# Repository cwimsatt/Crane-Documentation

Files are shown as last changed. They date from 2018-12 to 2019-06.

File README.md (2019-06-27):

---
description: Information on your M3D Crane Series printer.
---

# Welcome

Welcome and thank you for choosing the M3D Crane series of printers! This is the getting started / quick-start guide for the Crane Series 3D Printer. First select the Model style of M3D Crane you have purchased and you will be directed to the Quick Start Guide that matches your new printer.

NEW - July 2019 WalkThrough / Crash Course: For users setting up their quad head for the first time and looking to gain a deep understanding of the system to get the best results, start [here](https://coda.io/d/M3D-Official-Troubleshooting-Self-Help-Guide_dzE73kMbIAL/Quad-Expert-Crash-Course_sudLH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).

For troubleshooting please visit the [Self-help guide](https://coda.io/d/M3D-Public-Coda-Self-Help-Support_dzE73kMbIAL/Crane-Troubleshooting_suMmY#_lu4jO)

| \*\*\*\*[**The Crane Bowden**](https://crane.printm3d.com/crane-bowden-guide/crane-bowden-unboxing-assembly)\*\*\*\* | [**The Crane Dual**](https://crane.printm3d.com/crane-dual/unboxing-and-assembly)\*\*\*\* | \*\*\*\*[**The Crane Quad**](https://crane.printm3d.com/crane-quad-guide/unboxing-and-assembly)\*\*\*\* |
| :---: | :---: | :---: |

<table>
  <thead>
    <tr>
      <th style="text-align:center">
        gras
      </th>
      <th style="text-align:left">
        
        <p>
          test
        </p>
      </th>
      <th style="text-align:center">
        gras
      </th>
    </tr>
  </thead>
  <tbody></tbody>
</table>| Quick Links -- Bowden | Quick Links--Dual | Quick Links -- Quad |
| :---: | :---: | :---: |
| [Assembly Guide](https://crane.printm3d.com/crane-bowden-guide/crane-bowden-unboxing-assembly) | [Assembly Guide](https://crane.printm3d.com/crane-dual/unboxing-and-assembly) | [Assembly Guide](https://crane.printm3d.com/crane-quad-guide/unboxing-and-assembly) |
| [Network Setup](https://crane.printm3d.com/crane-bowden-guide/first-time-network-setup) | [Network Setup](https://crane.printm3d.com/crane-dual/first-time-network-setup) | [Network Setup](https://crane.printm3d.com/crane-quad-guide/first-time-network-setup) |
| [LCD Menu Navigation](https://crane.printm3d.com/crane-bowden-guide/lcd-menu-navigation) | [LCD Menu Navigation](https://crane.printm3d.com/crane-dual/lcd-menu-navigation) | [LCD Menu Navigation ](https://crane.printm3d.com/crane-quad-guide/lcd-menu-navigation)  |
| [Duet Web Control First Look](https://crane.printm3d.com/crane-bowden-guide/intro-to-duet-web-control) | [Duet Web Control First Look ](https://crane.printm3d.com/crane-dual/duet-web-control-first-look) | [Duet Web Control First Look](https://crane.printm3d.com/crane-quad-guide/first-look-at-duet-web-control-interface)  |
| [Bed Leveling](https://crane.printm3d.com/crane-bowden-guide/manual-bed-leveling) | [Bed Leveling](https://crane.printm3d.com/crane-dual/manual-bed-leveling-assistant)  | [Bed Leveling](https://crane.printm3d.com/crane-quad-guide/manual-bed-leveling-assistant) |
| [Bed/Nozzle Control](https://crane.printm3d.com/crane-bowden-guide/heating-the-bed-and-the-nozzle) | [Bed/Nozzle Control](https://crane.printm3d.com/crane-dual/heating-the-bed-and-the-nozzle) | [Bed/Nozzle Control](https://crane.printm3d.com/crane-quad-guide/heating-the-bed-and-the-nozzle) |
| [Loading/Unloading Filament](https://crane.printm3d.com/crane-bowden-guide/loading-and-unloading-filament) | [Loading/Unloading Filament](https://crane.printm3d.com/crane-dual/loading-and-unloading-filament) | [Loading/Unloading Filament](https://crane.printm3d.com/crane-quad-guide/loading-and-unloading-filament) |
| [Slicing your Model](https://crane.printm3d.com/crane-bowden-guide/slicing-and-printing-your-first-model) | [Slicing your Model](https://crane.printm3d.com/crane-dual/finding-and-slicing-your-model) | [Slicing your Model](https://crane.printm3d.com/crane-quad-guide/finding-and-slicing-a-model) |
| [Your First Print](https://crane.printm3d.com/crane-bowden-guide/first-print) | [Your First Print](https://crane.printm3d.com/crane-dual/first-print) | [Your First Print](https://crane.printm3d.com/crane-bowden-guide/first-print) |

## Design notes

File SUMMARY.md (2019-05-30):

# Table of contents

* [Welcome](README.md)
* [Warnings](warnings.md)
* [Coda For Troubleshooting](coda-troubleshooting.md)

## Crane Bowden Guide

* [Unboxing/Assembly](crane-bowden-guide/crane-bowden-unboxing-assembly.md)
* [First time Network Setup](crane-bowden-guide/first-time-network-setup.md)
* [LCD Menu Navigation](crane-bowden-guide/lcd-menu-navigation.md)
* [First look at Duet Web Control](crane-bowden-guide/intro-to-duet-web-control.md)
* [Bed Leveling](crane-bowden-guide/manual-bed-leveling.md)
* [Heating the Bed and the Nozzle](crane-bowden-guide/heating-the-bed-and-the-nozzle.md)
* [Loading and Unloading Filament](crane-bowden-guide/loading-and-unloading-filament.md)
* [Finding and Slicing a Model](crane-bowden-guide/slicing-and-printing-your-first-model.md)
* [First Print](crane-bowden-guide/first-print.md)

## Crane Quad Guide

* [Unboxing and Assembly](crane-quad-guide/unboxing-and-assembly.md)
* [First time Network Setup](crane-quad-guide/first-time-network-setup.md)
* [LCD Menu Navigation](crane-quad-guide/lcd-menu-navigation.md)
* [First Look at Duet Web Control Interface](crane-quad-guide/first-look-at-duet-web-control-interface.md)
* [Bed Leveling](crane-quad-guide/manual-bed-leveling-assistant.md)
* [Heating the Bed and the Nozzle](crane-quad-guide/heating-the-bed-and-the-nozzle.md)
* [Loading and Unloading Filament](crane-quad-guide/loading-and-unloading-filament.md)
* [Finding and Slicing a Model](crane-quad-guide/finding-and-slicing-a-model.md)
* [First Print](crane-quad-guide/first-print.md)

## Crane Dual

* [Unboxing and Assembly](crane-dual/unboxing-and-assembly.md)
* [First time Network Setup](crane-dual/first-time-network-setup.md)
* [LCD Menu Navigation](crane-dual/lcd-menu-navigation.md)
* [Duet Web Control First Look](crane-dual/duet-web-control-first-look.md)
* [Bed Leveling](crane-dual/manual-bed-leveling-assistant.md)
* [Heating the bed and the Nozzle](crane-dual/heating-the-bed-and-the-nozzle.md)
* [Loading and Unloading Filament](crane-dual/loading-and-unloading-filament.md)
* [Finding and Slicing Your Model](crane-dual/finding-and-slicing-your-model.md)
* [First Print](crane-dual/first-print.md)

## SD card and Firmware

* [Accessing Your SD Card](sd-card-and-firmware/accessing-your-sd-card.md)
* [SD card Structure](sd-card-and-firmware/sd-card-structure.md)
* [Firmware/Configuration](sd-card-and-firmware/updating-firmware.md)

## Advanced Tuning M3D Crane Series

* [Part Prints M3D Crane Series](advanced-tuning-m3d-crane-series/part-prints-m3d-crane-series.md)
* [Introduction to G-Code Commands](advanced-tuning-m3d-crane-series/beginner-introduction-to-g-code-commands.md)
* [Duet Web Control Bed Leveling Assistant](advanced-tuning-m3d-crane-series/duet-web-control-bed-leveling-assistant.md)
* [Important G-Code Commands](advanced-tuning-m3d-crane-series/important-g-code-commands.md)
* [Pro Tuning Guide](advanced-tuning-m3d-crane-series/tuning-guide.md)
* [Temperature Calibration](advanced-tuning-m3d-crane-series/temperature-calibration.md)
* [Adjusting Homing Macros](advanced-tuning-m3d-crane-series/adjusting-homing-macros.md)
* [Filament Extrusion Rate](advanced-tuning-m3d-crane-series/filament-extrusion-rate.md)
* [ABS-R Success Guide](advanced-tuning-m3d-crane-series/abs-r-success-guide.md)
* [In-Depth Z-System Sequencing and Alignment](advanced-tuning-m3d-crane-series/in-depth-z-system-sequencing-and-alignment.md)

## Community Submissions/Attributions

* [About Community Submissions](community-submissions-attributions/community-submissions.md)
* [User Submitted Guides](community-submissions-attributions/user-submitted-guides.md)
* [Attributions](community-submissions-attributions/attributions.md)

## Changelog

* [Changelog](changelog/changelog.md)

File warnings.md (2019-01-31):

# Warnings

Please read through all the warnings as they may save you from making a mistake that could result in injury to yourself or your M3D Crane Series printer. 

## Warnings

1. DO NOT TOUCH PRINTER WHILE OPERATING The Crane is a powerful machine. While the Crane is moving or printing you should not reach into the buildspace.
2. AVOID MOVING WITHOUT POWER
3. MOVE MOTORS/BED/EXTRUDER SLOWLY

   Moving motors generates power on all printers and can damage your board. There is no clear indicator of the power you are generating however when moving very fast the fans may start to turn. If you can hear the fan moving air, you're close to voltages that will break the duet regulator \(more than 28V\). Moving components about 50mm/s is safe. It is best to always move components while the system is powered.

4. DISABLING MOTORS

   When you disable motors the printhead may drop extremely slowly to the limit switch. This is normal behavior and requires rehoming.

5. ESD SAFETY:

   The Duet contains an ARM class 2 processor, we recommend you use a wrist straps when touching any wires that could send shocks to the main processor and fry it.

6. DON'T USE AN ESD WRIST STRAPS TIED TO A SURGE STRIP

   The printer is grounded. If you wire the strap wrong it can cause a short circuit through your body whenever you touch the printer.

7. USE UNDER SUPERVISION

   Use product in locations where nothing can catch on fire should the worst occur. The Crane is constructed out of metal and fireproof materials. Still, PLA and other filaments can burn fire if the printer is used improperly.

8. MAXIMUM EXTRUDER SPEED

   It is a common misconception that printhead travel movement speed \(i.e. 60 mm/s\) is the limiting factor when printing. However, it is extruder volumetric \(or mass\) flow rate that is the true limiting speed in most conditions. It is not easy to be able to exceed 9 mm^3/s \(PLA\) and 12 mm^3/s \(Higher temp materials like PETG, ABS\) except in special cases. To calculate flow rate multiple head speed, layer width, and layer height. For example: 45mm/s movement, 0.3 mm layers and 0.5 mm wide would be 6.75mm^3/s.

9. Z SPEED

   The bed current, acceleration and speed are configured for worse case scenarios like heavy prints. You can increase speeds when printing lighter items or depending on your application of the printer.

10. BED TEMPERATURE

    If you are using a glass print bed, give the printer an extra few minutes to reach temperature. In open air, the glass surface will be 5-10 C cooler than the bed temperature readouts from the thermistor.

11. FRAME CAN BE SHARP

    The frame of the printer is metal and could contain sharp edges. Use caution when moving the printer or moving around the printer. Keep your hands out of the machine during operation and be careful when lifting.

12. BURN HAZARD

    BED and NOZZLES are hot!

13. USE CAUTION WHEN REMOVING PRINTS

    The best strategy is to let the bed cool, most prints pop off by themselves.

14. REMOVING DUET SD CARD DISABLES FEATURES

    The Duet relies on its microSD card to serve as memory, storage for the LCD menu structure, duet webhost, and basic configurations. Without this card you can not connect over ethernet or use the LCD, however USB will still work. We do not recommend removing it. There is an SD card slot under the LCD providing a card slot physically moving print Gcode files, or use the web interface to upload Gcodes.

15. It should be noted that each Crane Series printer has a Voltage switch on the right hand side of the machine. For operation in the US the voltage must be set to 115.

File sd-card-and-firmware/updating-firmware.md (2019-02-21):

# Firmware/Configuration

It is very important that your M3D Crane Series printer has the most up to date software. In order to ensure the software is the newest version, you will need to identify what version of the software you are currently running. 

{% hint style="warning" %}
Always be sure your M3D Crane Series printer is powered OFF before removing the SD card. Always be sure the properly eject your SD card from your PC after installing the updates. 
{% endhint %}

## Identifying Firmware Version

In order to identify your Firmware version you will need to go into your **Duet Web Control Console** and select the **Settings** option on the left side of the screen. Under the General tab, all of the **Firmware Versions** are listed. 

Firmware Information listed in Settings

Once you have identified your software version and determined it is in need of an update follow this guide closely in order to successfully update your M3D Crane Series printer. These updates must be done in order. 

1. Firmware
2. Duet Web Control
3. Configuration Files

If you have an SD card reader, it is recommended that you simply remove the SD card from your M3D Crane Series printer, place it in your computer's SD card reader and drag and drop the Configuration updates. However the Firmware and the Duet Web Control files must be updated using the process described below. 

{% hint style="info" %}
Updating your firmware is important in order to obtain the latest features and bug fixes. The Duet Maestro board uses a fork of RepRap firmware to control a 3D printer. 
{% endhint %}

## Firmware:

Our firmware updates, courtesy of user dc42 can be found here: [https://github.com/dc42/RepRapFirmware/releases/tag/2.02RC5](https://github.com/dc42/RepRapFirmware/releases/tag/2.02RC5)

| Version  | Description  | Author  |
| :--- | :--- | :--- |
| 2.03 beta 2 | [System Firmware](https://github.com/dc42/RepRapFirmware/releases/download/2.03beta2/DuetMaestroFirmware.bin) | dc42 |
| 1.22.6 | [Duet Web Control](https://github.com/dc42/RepRapFirmware/releases/download/2.02/DuetWebControl-1.22.6.zip) | dc42 |

## Updating System Firmware

1. Download the firmware version linked above. This will be a _.bin_ or binary file called _**DuetMaestroFirmware.bin**_.
2. Go to the _**settings**_ tab of the Duet Web Console and find the ****_**Upload File\(s\)**_ button. Files uploaded here will be stored in the ****_**sys/**_ ****directory of the microSD card. Upload the _**DuetMaestroFirmware.bin**_ files.  
3. When the firmware upgrade is completed, you can visit the _**Settings**_ ****tab in order to ensure that the _**Firmware Version**_ has been updated. 

Upload Files Duet Web Control Console

## Updating Duet Web Console:

1. Download the Duet Web Control update linked above. This will be _**.zip**_ file. \(No need to unpack this .zip file as it will be uploaded as a .zip\)
2. Go to the _**Settings**_ tab of the Duet Web Console and find the _**Upload File\(s\) button.**_ Upload the _**DuetWebControl.zip**_ file. 
3. When the Duet Web Control console is finished updating it will automatically _**restart**_. Once it's restarted, you can go to the _**Settings**_ tab in order to ensure the Duet Web Control has been updated.  

Upload Files Duet Web Control Console

## Configuration Files:

These Configuration Files are for use with Duet Firmware 2.02RC5. This update is tested and official but still being actively updated. [https://github.com/PrintM3D/Crane/releases](https://github.com/PrintM3D/Crane/releases)

| Version | Description | Author |
| :--- | :--- | :--- |
| 2.02RC5: \(1.35\) | [M3D Crane Bowden](https://github.com/PrintM3D/Crane/releases/download/1.35-master/Crane_Bowden_135.zip) | M3D |
| 2.02RC5: \(1.35\) | [M3D Crane Dual ](https://github.com/PrintM3D/Crane/releases/download/1.35-master/Crane_Dual_135.zip) | M3D |
| 2.02RC5: \(1.35\) | [M3D Crane Quad](https://github.com/PrintM3D/Crane/releases/download/1.35-master/Crane_Quad_135.zip) | M3D |

## Configuration Updates via SD Card:

Updating the Configuration files involves copying the new versions of the configuration files to your M3D Crane Series printer's SD card. You will need an SD card reader in order to update the configuration files using this method. Be sure your M3D Crane Series printer is powered OFF before removing the SD card. The Configuration files that must be updated are **/sys/, /macros/**, and **/menu**. You may wish to back up your /macros/ in order to prevent any gcode files, slices, or macros you wish to save from being overwritten during the update process.  

1. Download the Configuration files appropriate to your M3D Crane Series printer. For this example we will show the process for M3D Crane Bowden. 
2. Power down your M3D Crane Series printer. Remove the SD card by pressing it firmly until you feel it release.
3. Insert the SD card into your SD card reader and open the SD drive on your PC. Now is the time to make backups of any files on your SD card you wish to keep. 
4. Open the folder containing the new Configuration files and copy them to the SD card. Replace and override when prompted. 

Download the Configuration file

Copy the Configuration files

Paste, or move Configuration files to the SD card

## Video Tutorial:

The following video tutorial is from our **User Submissions** made by **M3D Crane Series user Tylerun**. Our Firmware Updates are no longer in pre-release however once you've downloaded the new Firmware and Duet Web Control Updates from this page, following the remainder of the video tutorial will result in accurate updates.   

{% embed url="https://www.youtube.com/watch?v=hO7-jUEo5Q4" %}

##  

{% hint style="info" %}
**Warning: Updating your firmware can cause unintended consequences. Be aware that upgrading or downgrading to unstable firmware versions can cause unexpected bugs and issues. Use caution!**
{% endhint %}

## Other Resources

1. [Duet 3D Wiki: Updating and Installing Firmware](https://duet3d.dozuki.com/Wiki/Installing_and_Updating_Firmware)
2. [Duet3D Forum](https://forum.duet3d.com/): For firmware and Duet specific questions
3. [Duet Fork of RepRap Firmware](https://github.com/dc42/RepRapFirmware)

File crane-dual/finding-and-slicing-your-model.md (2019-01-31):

# Finding and Slicing Your Model

## Slicing and Printing the first model: 

You may choose to create your own 3D models with software such as [Autodesk's Fusion 360](https://www.autodesk.com/products/fusion-360/overview), or [Openscad](http://www.openscad.org/downloads.html), however you may wish to start printing models that are already available for download. You can find free models for 3D printing at [Thingiverse](https://www.thingiverse.com/), or you can try a few from [this list](https://all3dp.com/1/free-stl-files-3d-printer-models-3d-print-files-stl-download/).



Once you have found your ideal 3D model and downloaded it's **STL** file, it's time to download a **Slicer**. A **slicer** takes a 3D drawing \(most often in .STL format\) and translates this model into individual layers. It then generates the machine code \(g.code\) that the **printer** will use for **printing**.

While there are several great Slicers out there, both free as well as paid we recommend [Cura](https://ultimaker.com/en/products/ultimaker-cura-software). Download and install the latest version of **Cura by Ultimaker**. Cura will provide a wizard so that you can add your M3D Crane Series printer's dimensions and nozzle diameter.



The M3D Crane Bowden has several Cura **Printing Profiles** that have been pre-configured, each to the optimal settings within Cura for a selection of different material types. You can find and download the first of those here within this point release: [https://github.com/PrintM3D/Crane/releases/tag/1.1](https://github.com/PrintM3D/Crane/releases/tag/1.1) -- you can also find the latest version of the Crane Series SD Card here in case you need it.

## Setting up your Slicer:

Once you have selected and downloaded the Cura Printing Profile you will need for the material you are printing in, you can **Import the profile into Cura and Save it.** You can find these options in the Menu Bar at the top of the slicer's window. For additional information on Cura settings please go [here](https://ultimaker.com/en/products/ultimaker-cura-software).

Once you have downloaded your preferred slicer you can follow the steps below to see how to set up the slicer with the correct printer settings. For this example we'll be using Cura.

### Cura: 

 Open Cura's Setting by pressing **Preferences &gt; Configure Cura**_...._

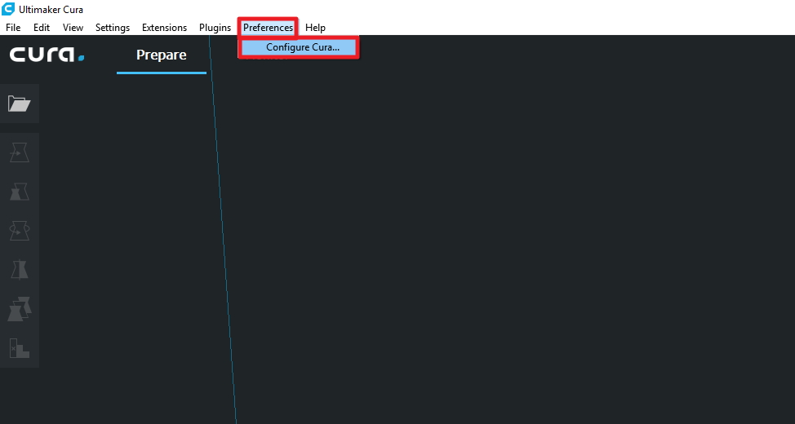
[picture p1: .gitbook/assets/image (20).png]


 Once you have opened Cura's settings we will go to **add a printer**. This is because we need to tell Cura the specifics of our printer, such as the maximum build volume of the printer. Press _**Printers**_ and then **Add** in order to add a new printer. This will open a new window.

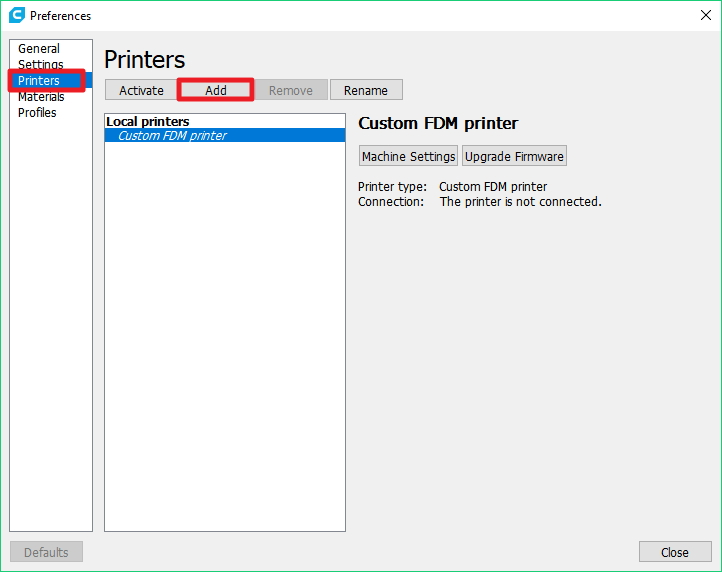
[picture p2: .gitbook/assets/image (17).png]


Next, press **Custom**_._ This indicates we are adding a custom printer to Cura's loadout. You can define the **Printer Name** however you want. Then press **Add Printer**_,_ this should open another setting window_._

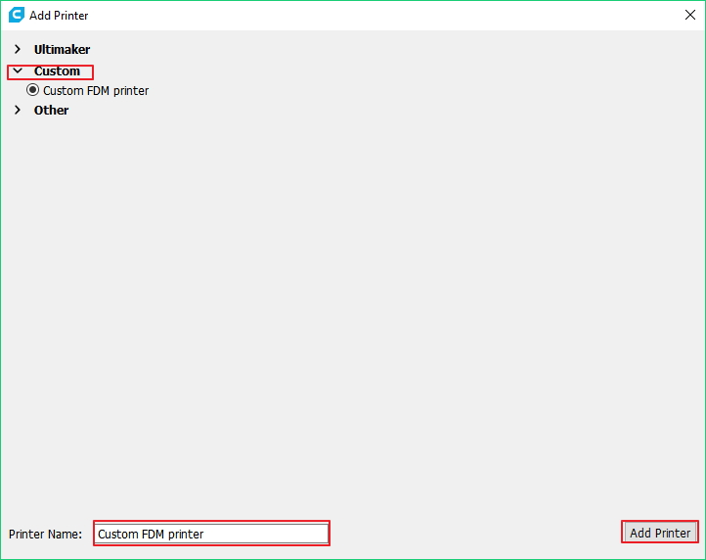
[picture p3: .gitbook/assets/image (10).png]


This window allows you to **configure the printer settings** of your M3D Crane Series printer. This informs Cura of the M3D Crane Series printer's build space, the firmware flavor and specifies starting and ending G-code.

The **build volume** of the printer represents the **maximum value that the printer can travel in each direction**.

 The **firmware flavor** is the type of firmware that the board is running. The Duet Maestro board runs on **RepRap firmware**. Your firmware flavor indicates what type of commands the board can understand.

The **starting and ending G-code** is a series of commands that are run at the start and at the end of every print. This is important as it allows you to retract your filament after the print and turn all the heaters off.

**Don't click** _**Close**_ **just yet!** Move on to the **Extruder 1** tab and fill in the following information. Fill in the **nozzle diameter and the material diameter**. Your nozzle diameter may vary in the future as you mount different types of nozzles on your M3D Crane Series Printer. Then you can click **Close.**

Once you have added the printer make sure to activate it by selecting the name and then clicking the button **Activate**_._

### Importing the Printer Profile 

In Cura, open the Preferences again by clicking _Preferences &gt; Configure Cura._ Click _Profiles &gt; Import_. Then a window will pop up that will allow you to navigate to the profile you just downloaded. It will most likely be in the _Downloads_ folder.

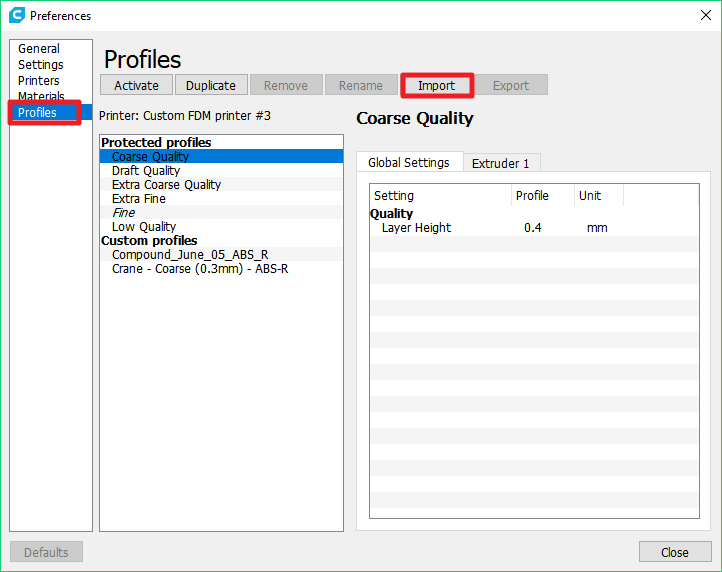
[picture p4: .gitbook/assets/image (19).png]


Once you have properly imported the file you will have to **Activate** it. Select the profile and click the button **Activate**_._ The print settings you just downloaded have now been applied to Cura. Whenever you slice a model, it will now incorporate these settings.

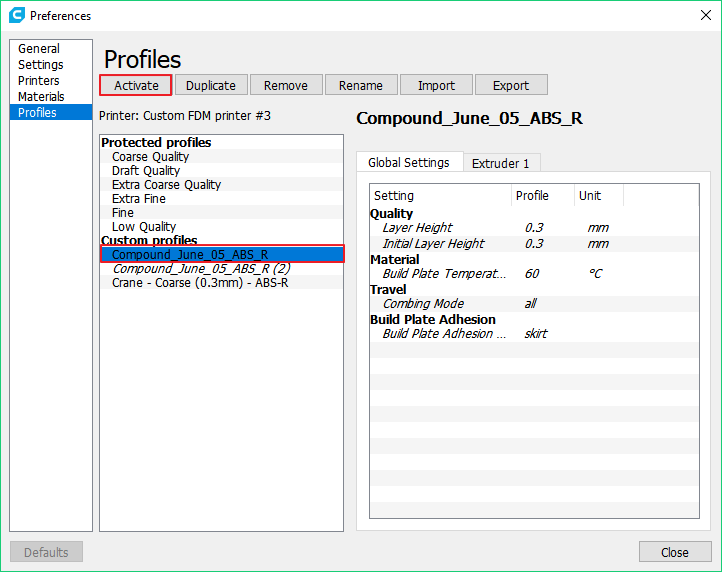
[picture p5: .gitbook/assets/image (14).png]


## Slicing your Model 

Slicing your model is an extremely important step. Most slicer software allow you to control different print settings such as layer height or print speed in order to change how you print. Slicing has great effect on the quality of your print you produce. For additional information on Cura settings please go [here](https://ultimaker.com/en/products/ultimaker-cura-software).

Now that your settings are optimized with the imported printer profile, you can slice your model. Simply click the "**prepare to print**" button in the lower right corner of the slicer to generate your g.code. **Save this new file to your computer.**

Your model is now saved on your hard drive. Just follow the instructions for how to use your [Duet Web Control Interface](https://crane.printm3d.com/crane-bowden-guide/intro-to-duet-web-control), to learn how to upload your new gcode file. Enjoy watching your models come to life!

The possibilities of what you can do with your M3D Crane Dual are seemingly endless now that you know how to create, or find 3D models and how to prepare them to be printed. Next you will learn how to start your first 3D print! Follow the guide to the next section where you will find instructions on how to print.

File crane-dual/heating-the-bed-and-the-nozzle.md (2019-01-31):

# Heating the bed and the Nozzle

{% hint style="info" %}
There are several options available to control your M3D Crane Series printer. We recommend using the menus provided within the Duet Web Control Interface, however you can also control it via the gcode tab within the Duet Web Control Interface by typing in gcode commands directly, or you can control your M3D Crane Series printer manually through the menu on the LCD screen. This guide will focus on using the menu options inside the Duet Web Control Interface. The other options will be covered elsewhere in the guide.
{% endhint %}

## Using Duet Web Control Interface to Heat the print bed: 

{% hint style="warning" %}
Prior to every heating of the nozzles or the bed, check the temperature readouts in the _Current_ column on the Duet Web Console. These values should be in the 20°C - 250°C. A value of 2000°C, indicates a problem in the wiring of the thermistor. Fix the issue prior to activating the heaters.
{% endhint %}

Connect to your **Duet Web Control Interface** via your network using the **IP address** your M3D Crane Series printer displayed during the network setup step. Once you are connected, you can proceed to heating up your printer bed.

In the **Duet Web Console Interface** find the table: _**Tools/Heaters/Extra**_ pictured below. In the row **Bed** **change the active temperature** from 0C to your **desired temperature** and press **Enter**.

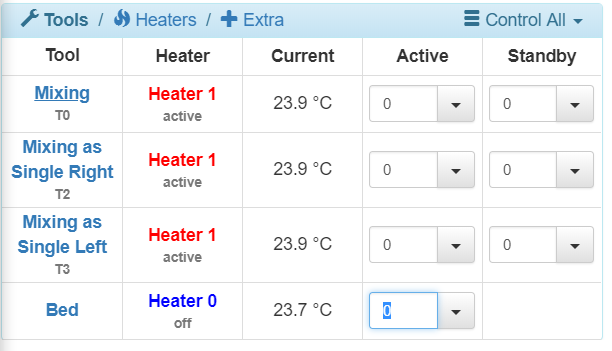
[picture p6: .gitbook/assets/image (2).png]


In order to turn the heated **bed off,** set the temperature back to **0** in the **Active** column and press **Enter**.

{% hint style="info" %}
It can take a few minutes for the bed to reach the desired temperature and for the heat to dissipate.
{% endhint %}

You can monitor the heating of your bed in both the **Tools** as well as the **Temperature Chart** sections of the Duet Web Control Interface. The Current column within the Tools section will display the temperatures as they change, and the chart will show you the temperature progression allowing you to easily spot any unwanted spikes or drops in the bed or nozzle.



## **Heating the Nozzles with Duet Web Console:** 

In the **Duet Web Control Interface** find the table **Tools/Heaters/Extra**, pictured below. You will be selecting **Tool 0**, which represents your nozzle. Once your tool \(**Tool 0**\) is selected, simply change the **Active temperature from 0C to your desired temperature**.

{% hint style="info" %}
Remember that the tool will only heat up to your set active temperature when the tool is **selected**.
{% endhint %}



In order to **turn off the heater,** set the tools **active temperature to 0 and press Enter**. Remember that a tool will heat up to the standby temperature when the tool is not selected, but was previously selected. You can see which tool is activated by the underline of the tool name in the Duet Web Console.

Now you know the basics of heating your bed and nozzle it's time to move on to loading and unloading filament! Move on to the next section to learn how to load and unload your M3D Crane Dual printer.

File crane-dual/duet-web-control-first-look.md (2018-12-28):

---
description: >-
  In this page you'll get a basic understanding of the Duet Web Control and set
  up your first print.
---

# Duet Web Control First Look

## Getting to know your Duet Web Control Interface:  

Now that the **Network Setup** is complete and you have arrived at the IP address your M3D Crane Series printer displayed during the Network Setup process, you can start to utilize the **Duet Web Control Interface**. There are many aspects you are able to monitor and control before, during and after printing from the Duet Web Control Interface. Here we will go over just the basics needed to get you up and printing as quickly as possible.

The Duet Web Control Interface provides a comprehensive way to monitor and make changes to nearly all aspects of your 3D printing process. This guide is focused on getting your M3D Crane Series printer up and printing quickly. Links will be provided at the end of this tutorial to allow a more in-depth understanding of all the various functions of the Duet Web Control Interface.

## Duet Web Control Interface First Look:  



## The upper portion of the Duet Web Control Interface will display real time information:  



The **Machine Status** section displays the **current axis positions, extruder drive positions, Speeds and Z-probe reading**.

Machine Status

The **Tools** section provides a place to input and monitor the **temperature** of the various tools such as the **nozzle** and the **bed**.

Tools

The **Temperature Chart** section will provide a real time chart showing the **temperature increase and decrease of the bed and the nozzle**.

Temperature Chart

## The Lower portion of the Duet Web Control Interface is Dynamic:  



It contains the **Main Menu Section**, which is comprised of tabs that display their information/interface in the middle portion of the lower half of the Duet Web Control Interface. Under the Machine Control tab you can find the **Axes and extruder control.** The Lower left portion contains the **User-Defined Macros** section.

Main Menu

## Print Status Tab:  

The **print status tab** will not display any information until a print is started, but once you have uploaded and started a print you will see **real time progress** as well as be able to **make changes in real time** to your print as it's printing, such as **micro stepping** or using the **Fan Control section**, changing **fan speeds and ratios.**

Print Status Tab

The **Print control** section enables you to **pause, cancel or resume** a print, and allows you to make small adjustments to the Z axis called **Z baby stepping**.

Print Control

The **File information** section **displays select information about the gcode file you have uploaded** to print.

File Information

These are the very basics of the Duet Web Control Interface. We'll go over more about the Macro function during the Bed Leveling Assistant section of this guide, but for more comprehensive and in-depth information on each of the features of the Duet Web Control Interface, click [HERE](https://duet3d.dozuki.com/Wiki/Duet_Web_Control_Manual#Section_Overview).

Now that you are more familiar with the Duet Web Control Interface, it's time to move on to the hands on work of leveling your M3D Crane Dual's print bed. In the next section we will cover a simple Basic Leveling method.

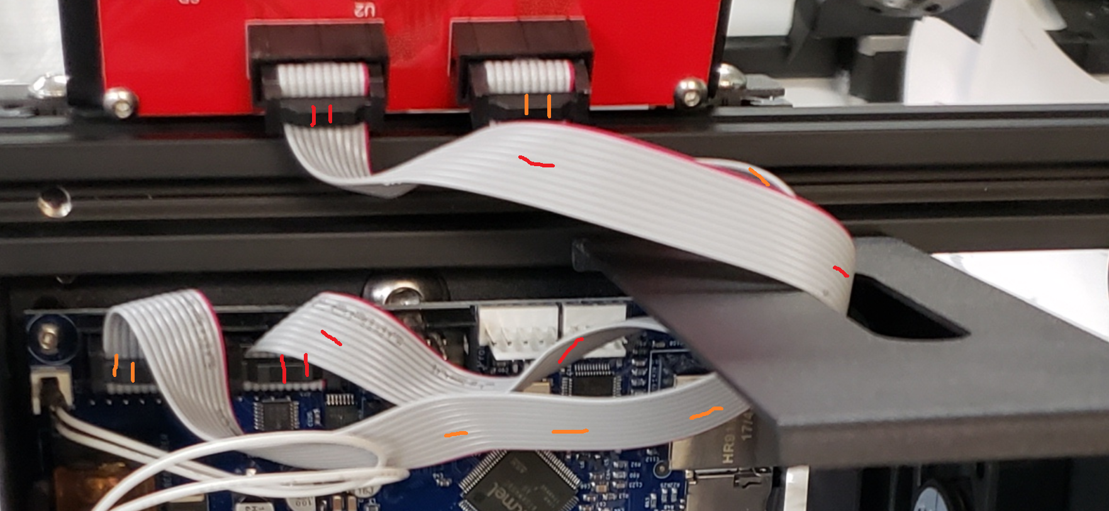
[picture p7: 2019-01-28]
.gitbook/assets/lcdconnection.png

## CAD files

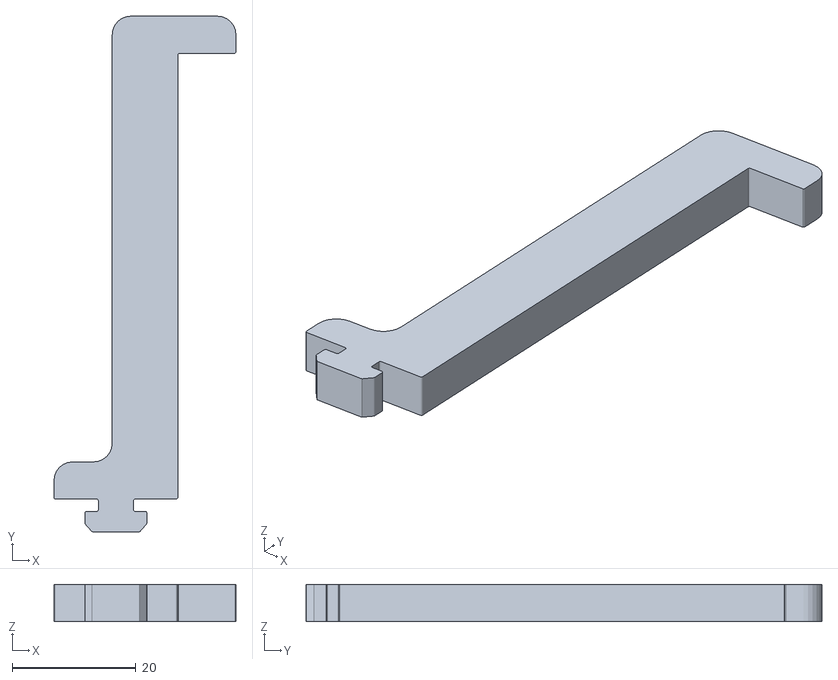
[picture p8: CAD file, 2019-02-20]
.gitbook/assets/078802_b1_crane_spool_holder-1.stl
29.4 x 83.3 x 6.00

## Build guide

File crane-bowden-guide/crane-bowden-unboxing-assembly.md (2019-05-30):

# Unboxing/Assembly

{% hint style="warning" %}
The M3D Crane Bowden contains sensitive electronics, delicate mechanical parts, and an electrical heating system. Please exercise all applicable safety precautions and follow this guide closely to avoid damage to your M3D Crane Bowden, to avoid injury to yourself or others, and insure proper operation. Check your Local Supply Voltage and set your printers Voltage accordingly, or risk damage to your printer.
{% endhint %}

## Setting up after unboxing your printer:  

After removing your M3D Crane Bowden from the box, remove all the plastic wrapping being careful not to cut any of the sensitive parts of the device, such as the cables. Your M3D Crane Bowden should look like this:



Remove the bolts at the bottom of each upright rail, as shown below. Setting them aside briefly:

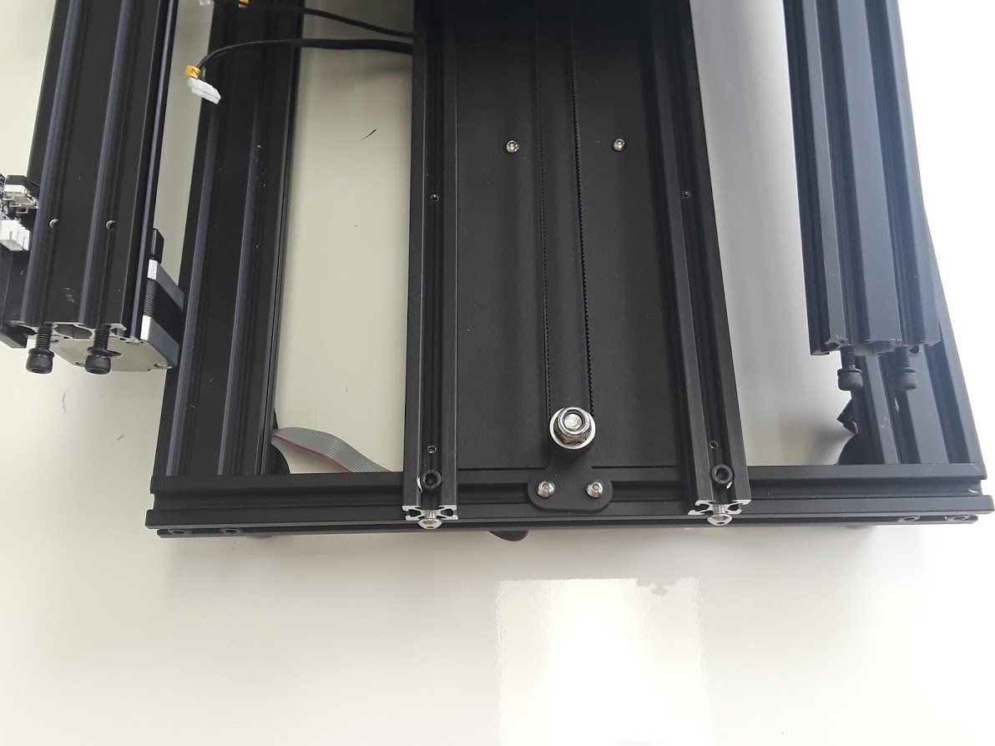
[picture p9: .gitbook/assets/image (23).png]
note the bolts sticking out of the rails


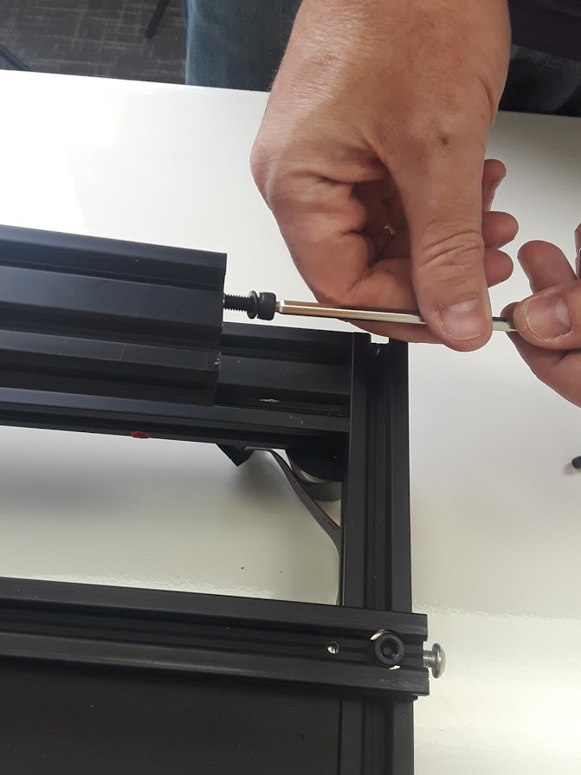
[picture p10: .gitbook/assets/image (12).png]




{% hint style="warning" %}
Inspect your M3D Crane Bowden for any damage that may have occurred during shipping. Every precaution has been made to prevent this, however it is advisable to give all the components a thorough inspection before operation. If any issues are discovered, document the damage by taking an image of the affected area and contact M3D immediately.
{% endhint %}

As long as no issues are discovered, you are ready for mechanical assembly.

## Assembly:  

Being careful not to stress or pull any of the cables, have a friend assist you in raising the upright rails; be sure to **align the bolt holes**.

If you aren't able to hold the upright in place, get someone's help to steady it. Line up the bolt holes\(that previously housed the bolts you removed\) and begin slowly tightening the bolts; first hand tighten, then slowly tighten more firmly with the provided **Allen Key**.



Ensure that all motor cables are connected. These are part of the **black ribbon cable**. You can identify the correct motor cable by looking at the **yellow tags reading 'X, Y, and Z'.** The motor connections are made up of 4 wires, while the associated endstop cable is a three wire cable directly beside the 4-wire cable for the respective motor; the only motor without an endstop is the extruder.





Connect the two gray ribbon cables labeled '1' and '2' and connect them to their respective ports on the back of the LCD assembly, 'EXP1' and 'EXP2'. **Be careful not to cross these connections as it may damage the LCD Screen.**





Should you find that your LCD cables are not labeled, simply determine which cable is **shortest**, that will be the cable to be connected to **EXP1**.

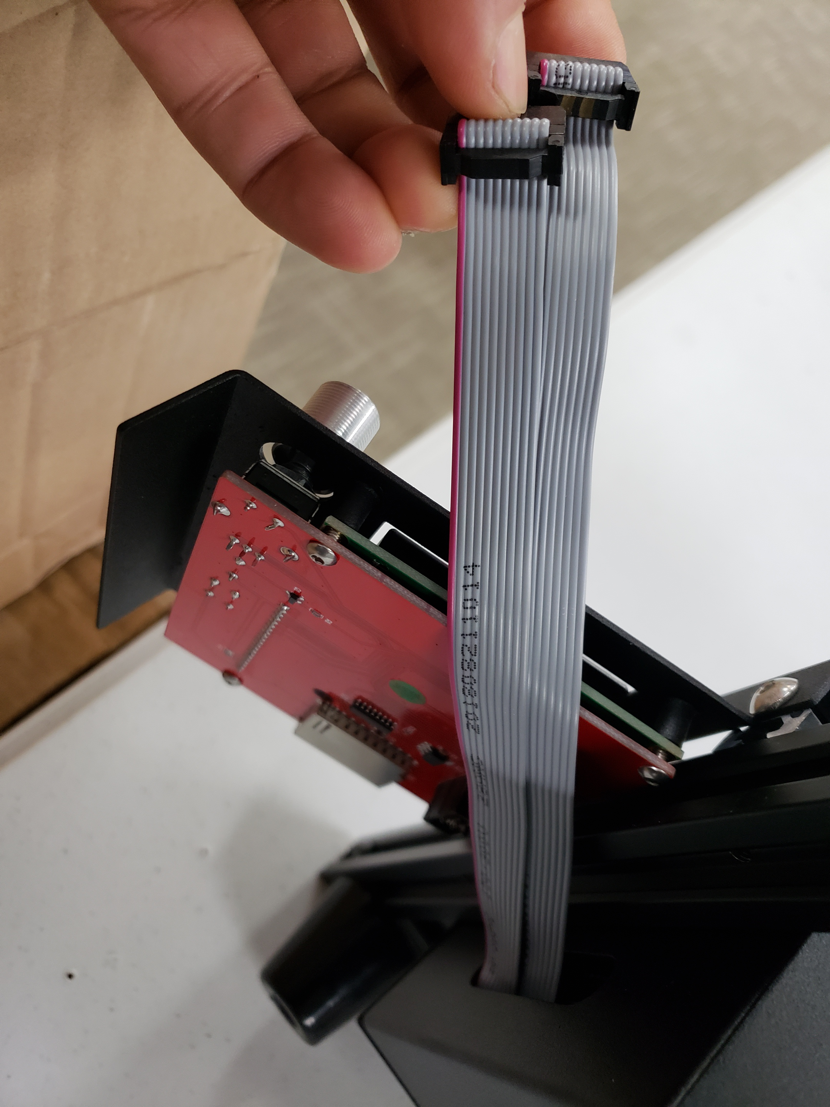
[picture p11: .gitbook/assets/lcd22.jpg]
Determine which is Shortest


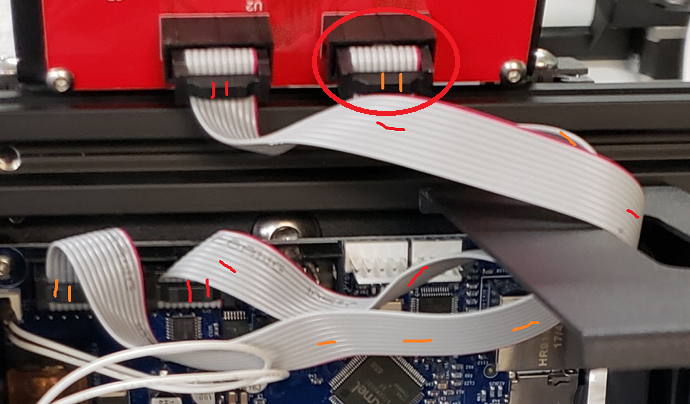
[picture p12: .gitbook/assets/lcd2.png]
EXP1


Connect the **short cable to EXP1**, plug the **longer** **cable into EXP2**, and proceed to the next step.

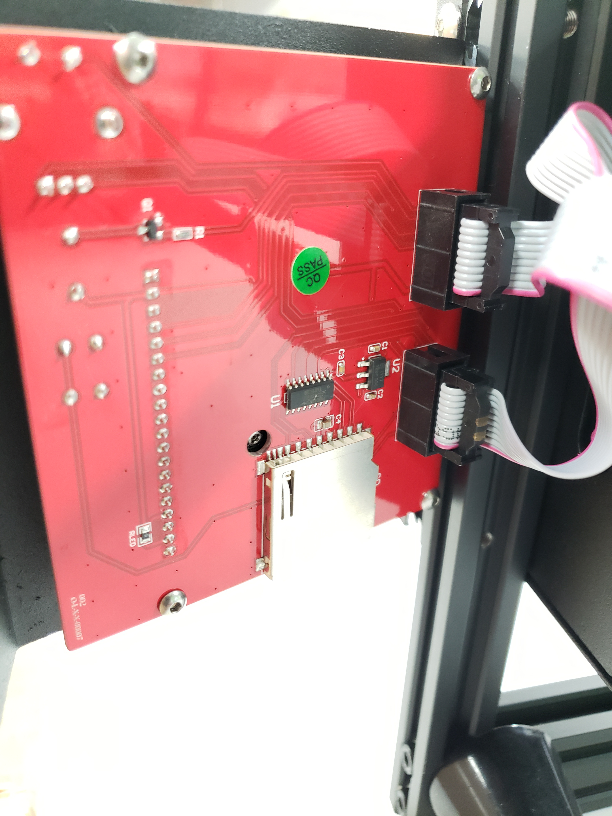
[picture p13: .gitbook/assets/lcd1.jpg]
Plug the Short Cable into EXP1 and the Long Cable in EXP2


After making the connections, use the provided bolts and Allen Key to secure the LCD to the front of the M3D Crane Bowden.



## Z-endstop positioning:

Be sure your M3D Crane is powered off and/or unplugged before you begin this step.

In order to ensure nothing is damaged during shipping, and furthermore during the first power on of your M3D Crane, it's been shipped with the Z-endstop raised. You will need to manually lower your Z-endstop before printing.

Z endstop

The first step to moving your Z-endstop to an appropriate height is to examine the exposed bolts below the Y-carriage and to tighten/loosen all four of your bed nuts so that only about 8-10 threads are exposed on each. You can see in this photograph a bolt that has been tightened to its recommended position. Use your own 7mm or 1/4th inch wrench to ensure each bolt is adjusted to approximately the same position.

8-10 threads exposed

Next you will need to manually center the print head over the bed. To do this gently move the print head left-to-right along the X-axis until it's in the center. Then, move the bed forward along the Y-axis until its center. At this point, the print head should be above the center of the bed. Finally, rotate the coupler between the Z-motor and the Z-leadscrew counter-clockwise until the left bracket of the X-axis is resting on top of the Z-endstop switch as seen in the photo.

Rotate the Coupler between the Z-motor and the Z-leadscrew

left bracket of the X-axis is resting on top of the Z-endstop switch

The Z endstop is attached to the rail with two T-nuts that hang the inside of the aluminum extrusion channel. Loosen the Z endstop bracket enough to loosen the 2 screws that secure the bracket to the rail.

After loosening the Z-endstop and allowing it to move down, we are now free to move the printhead closer to the bed. Slowly lower the print head until the nozzle touches the bed.

Little by little raise the Z endstop until a click is heard/felt and then tighten down the 2 screws again. You should be able to secure one of the nuts fairly easily to maintain the position of the Z endstop.

Manually raise your print head by rotating the Z axis and now you are ready to power on the M3D Crane and select Home All in the LCD menu. While it is still necessary that we run through the leveling process with the printer powered on, making these changes ensures that we do not cause any damage to the print surface.

In order to assure your M3D Crane Series printer maintains an accurate bed level after following the [Bed Leveling](https://crane.printm3d.com/~/edit/drafts/-LTi556ASBKSVfOwPujM/crane-bowden-guide/manual-bed-leveling) section of this guide it may be necessary to make further adjustments to the Z endstop position. Maneuvering the Z endstop in conjunction with following the Bed Leveling guide will lead to a more accurate and level print bed.

## X Bracket Alignment and tightening:

Should you notice your x bracket, the plate attaching the print head to the x axis is loose OR too tight follow the instructions in the pro-tuning guide to learn how to loosen or tighten the eccentric nuts that secure the x bracket to it's axis.

[https://crane.printm3d.com/advanced-tuning-m3d-crane-series/tuning-guide](https://crane.printm3d.com/advanced-tuning-m3d-crane-series/tuning-guide)

Should your x bracket appear warped or bent, please be sure to check that the eccentric nuts are not too tight. It should be secure enough so that then print head doesn't move around during printing about 1/16-1/12th turn extra past this point on the eccentric nuts should be sufficient any tighter could result in the appearance of warping or bending of the x bracket. Loosing these eccentric nuts should remedy this.

## Rubber Feet:

If your Crane is shipped without the feet assembled, please follow this videio instruction guide

{% embed url="https://photos.app.goo.gl/GswVwPuHoBw8vemBA" caption="" %}

## Spool Holder:

The M3D Crane Series comes equipped with a heavy duty spool holder. This Spool Holder well suited to hold the larger spools of 500 or 1000 feet of Filament. Here we show how to assemble the Spool Holder:

Spool Holder for larger spools of 3DInk Filament

The Spool Holder is comprised of the following parts:

* 2 T-nuts
* Mounting Bracket
* Spool Mount Spindle
* 2 End Caps

Spool Holder components

To assemble the Spool Holder screw the T-nuts into the holes at the bottom of the Mounting Bracket. Be sure to leave them fairly loose as you will tighten them firmly once the Mounting Bracket has been attached to the top rail of your M3D Crane Bowden printer.

T-nuts in place at the bottom of the Mounting Bracket

Once the T-nuts are in place, slip one end of the Spool Mount Spindle through the large hole in the top of the Mounting Bracket and secure with an End Cap.

End Cap in place to secure Spindle to Mounting Bracket

The Spool Holder is designed so that the End Cap secures the spool and prevents it from slipping off the Spool Mount Spindle while in use. When not in use it's advised to keep the End Cap secured to the Spool Mount Spindle to prevent it from becoming lost or misplaced.

Fully Assembled Spool Holder

Once your Spool Holder is fully assembled simply slip the T-nuts into the grove on the top rail of your M3D Crane Bowden printer and tighten securely.

{% hint style="danger" %}
Prior to exiting this section, please double check all connections, and place your crane on a flat surface. Ensure the Power Switch is Off\(O\), double check that your voltage is set appropriately for YOUR area\(consult local authorities if you are unsure\). **Failure to do this can irreparably harm the electronics in your printer.**
{% endhint %}

## Finished M3D Crane Bowden:

Once your M3D Crane Bowden is complete it should look like this:

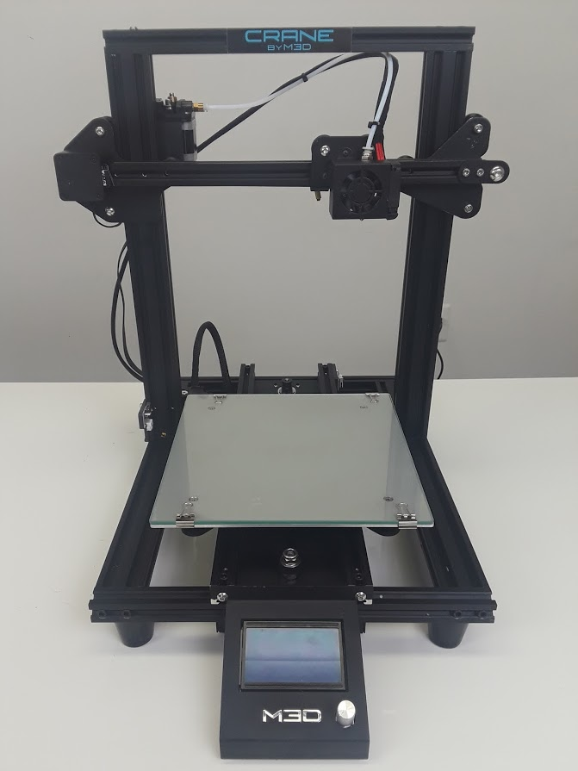
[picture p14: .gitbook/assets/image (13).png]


## Endstop Damage:

{% hint style="info" %}
Occasionally things can be damaged during shipping, and or come loose. If you notice that one of your end-stops has broken, you can swap any of the others to replace the Z end-stop as this one is the most important.
{% endhint %}

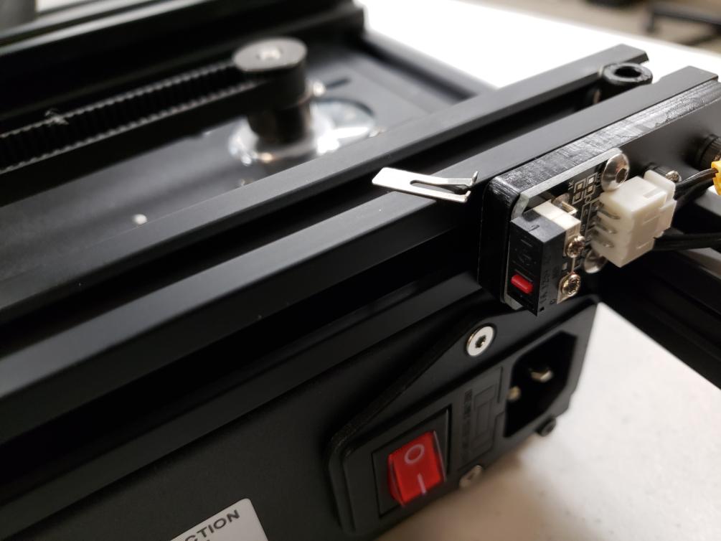
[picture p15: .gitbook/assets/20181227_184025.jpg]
Endstop damage during shipping


## Before powering on your M3D Crane Series Printer:

You should have received along with your printer, a micro SD card as well as a blue micro SD card adapter. Check the SD card slot on the right side of your Crane Series printer to see if yours was shipped with the SD card already in place. If your SD card is already in place, remove it and replace it before powering it on. The SD card may have been shifted or impacted during shipping and turning on the power with the SD card askew inside could lead to damage.

If your SD card has arrived in a small separate case, simply remove the SD card from it's package and place it into the SD card slot on the right side of your Crane Series printer.

The Crane Series of printers are unique in that they are built with a Duet Maestro board. The Duet board uses the information on the SD card to operate, in a sense the SD card that goes in the slot on the Duet acts like it's hard drive. It is for this reason that should you desire to use an SD card to move your gcode to your printer instead of using Duet Web Control, it's recommended to purchase a second micro SD card and use the SD card slot on the back of the LCD screen.

## Additional information:

After assembly you may have some questions that might be further discussed in our[ Pro Tuning Guide](https://crane.printm3d.com/advanced-tuning-m3d-crane-series/tuning-guide).

Congratulations!! You have completed the Assembly of your M3D Crane Bowden Printer!! In the next section you will learn how to include your new M3D Crane Bowden into your existing network, or set up a network from scratch.

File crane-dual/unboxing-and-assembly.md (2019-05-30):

# Unboxing and Assembly

{% hint style="warning" %}
The M3D Crane Dual contains sensitive electronics, delicate mechanical parts, and an electrical heating system. Please exercise all applicable safety precautions and follow this guide closely to avoid damage to your M3D Crane Dual, to avoid injury to yourself or others, and insure proper operation.

Check your Local Supply Voltage and set your printers Voltage accordingly, or risk damage to your printer.
{% endhint %}

## Setting up after unboxing your printer:  

After removing your M3D Crane Dual from the box, remove all the plastic wrapping being careful not to cut any of the sensitive parts of the device, such as the cables. Your M3D Crane Dual should look like this:



Remove the bolts at the bottom of each upright rail, as shown below. Setting them aside briefly:

note the bolts sticking out of the rails





{% hint style="warning" %}
Inspect your M3D Crane Dual for any damage that may have occurred during shipping. Every precaution has been made to prevent this, however it is advisable to give all the components a thorough inspection before operation. If any issues are discovered, document the damage by taking an image of the affected area and contact M3D immediately.
{% endhint %}

As long as no issues are discovered, you are ready for mechanical assembly.

## Assembly:  

Being careful not to stress or pull any of the cables, have a friend assist you in raising the upright rails; be sure to **align the bolt holes**.

If you aren't able to hold the upright in place, get someone's help to steady it. Line up the bolt holes \(that previously housed the bolts you removed\) and begin slowly tightening the bolts; first hand tighten, then slowly tighten more firmly with the provided **Allen Key**.



Ensure that all motor cables are connected. These are part of the **black ribbon cable**. You can identify the correct motor cable by looking at the **yellow tags reading 'X, Y, and Z'.** The motor connections are made up of 4 wires, while the associated endstop cable is a three wire cable directly beside the 4-wire cable for the respective motor; the only motor without an endstop is the extruder.





Connect the two gray ribbon cables labeled '1' and '2' and connect them to their respective ports on the back of the LCD assembly, 'EXP1' and 'EXP2'. **Be careful not to cross these connections as it may damage the LCD Screen.**





Should you find that your LCD cables are not labeled, simply determine which cable is **shortest**, that will be the cable to be connected to **EXP1**.

Determine which is Shortest

EXP1

Connect the **short cable to EXP1**, plug the **longer** **cable into EXP2**, and proceed to the next step.

Plug the Short Cable into EXP1 and the Long Cable in EXP2

After making the connections, use the provided bolts and Allen Key to secure the LCD to the front of the M3D Crane Dual.



## Z-endstop positioning:

Be sure your M3D Crane is powered off and/or unplugged before you begin this step.

In order to ensure nothing is damaged during shipping, and furthermore during the first power on of your M3D Crane, it's been shipped with the Z-endstop raised. You will need to manually lower your Z-endstop before printing.

Z endstop

The first step to moving your Z-endstop to an appropriate height is to examine the exposed bolts below the Y-carriage and to tighten/loosen all four of your bed nuts so that only about 8-10 threads are exposed on each. You can see in this photograph a bolt that has been tightened to its recommended position. Use your own 7mm or 1/4th inch wrench to ensure each bolt is adjusted to approximately the same position.

8-10 threads exposed

Next you will need to manually center the print head over the bed. To do this gently move the print head left-to-right along the X-axis until it's in the center. Then, move the bed forward along the Y-axis until its center. At this point, the print head should be above the center of the bed. Finally, rotate the coupler between the Z-motor and the Z-leadscrew counter-clockwise until the left bracket of the X-axis is resting on top of the Z-endstop switch as seen in the photo.

Rotate the Coupler between the Z-motor and the Z-leadscrew

left bracket of the X-axis is resting on top of the Z-endstop switch

The Z endstop is attached to the rail with two T-nuts that hang the inside of the aluminum extrusion channel. Loosen the Z endstop bracket enough to loosen the 2 screws that secure the bracket to the rail.

After loosening the Z-endstop and allowing it to move down, we are now free to move the printhead closer to the bed. Slowly lower the print head until the nozzle touches the bed.

Little by little raise the Z endstop until a click is heard/felt and then tighten down the 2 screws again. You should be able to secure one of the nuts fairly easily to maintain the position of the Z endstop.

Manually raise your print head by rotating the Z axis and now you are ready to power on the M3D Crane and select Home All in the LCD menu. While it is still necessary that we run through the leveling process with the printer powered on, making these changes ensures that we do not cause any damage to the print surface.

In order to assure your M3D Crane Series printer maintains an accurate bed level after following the [Bed Leveling](https://crane.printm3d.com/~/edit/drafts/-LTi556ASBKSVfOwPujM/crane-bowden-guide/manual-bed-leveling) section of this guide it may be necessary to make further adjustments to the Z endstop position. Maneuvering the Z endstop in conjunction with following the Bed Leveling guide will lead to a more accurate and level print bed.

## X Bracket Alignment and tightening:

Should you notice your x bracket, the plate attaching the print head to the x axis is loose OR too tight follow the instructions in the pro-tuning guide to learn how to loosen or tighten the eccentric nuts that secure the x bracket to it's axis.

[https://crane.printm3d.com/advanced-tuning-m3d-crane-series/tuning-guide](https://crane.printm3d.com/advanced-tuning-m3d-crane-series/tuning-guide)

Should your x bracket appear warped or bent, please be sure to check that the eccentric nuts are not too tight. It should be secure enough so that then print head doesn't move around during printing about 1/16-1/12th turn extra past this point on the eccentric nuts should be sufficient any tighter could result in the appearance of warping or bending of the x bracket. Loosing these eccentric nuts should remedy this.

## Rubber Feet:

If your Crane is shipped without the feet assembled, please follow this videio instruction guide

{% embed url="https://photos.app.goo.gl/GswVwPuHoBw8vemBA" caption="" %}

## Crane Spool Holder:

This new Spool Holder design is much more simple. It's a **SINGLE** small spool holder, which is meant to slip into the back facing groove in the top rail of your M3D Crane Series printer. You can print just one, however we do recommend you print up to 4. Having the Spool Holders as singles allows for more mobility, you can now move each spool holder along the axis so as to help control the filament's path to the Dual print head.

### Spool Holder 2.1

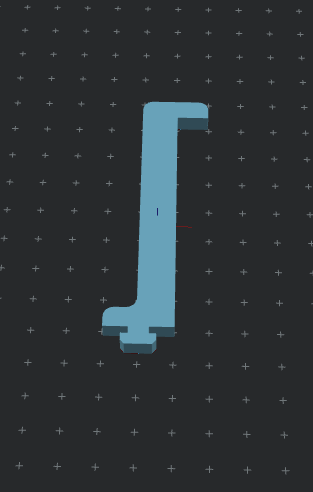
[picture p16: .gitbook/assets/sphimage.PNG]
Spool Holder 2.1


There is the original Spool Holder design meant to hold up to 4 Micro Spools.

### Spool Holder 1.0

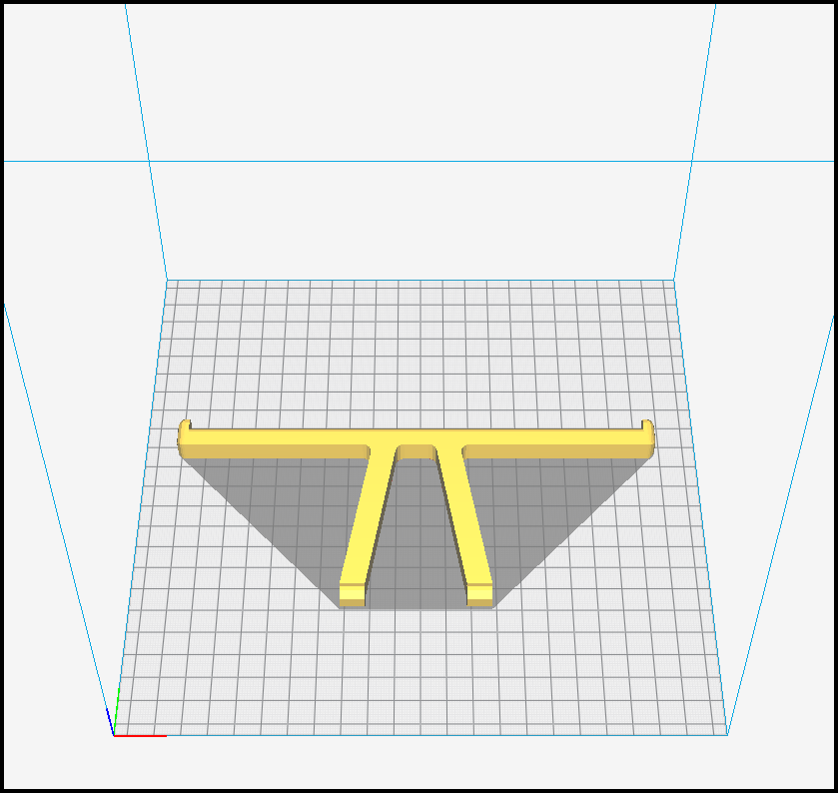
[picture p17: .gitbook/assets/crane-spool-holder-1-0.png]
Spool Holder 1.0


### **Additional Information:**

**It is not necessary to print the Spool Holder using CMYK filament**, in fact it's recommended you use the spool holder as one of your first "test prints". This will allow you to accurately calibrate your machine, make sure it's level and is printing properly using a filament you are most comfortable with such as a generic PLA for example.

You can also download [both Crane Spool Holder STL files](https://coda.io/d/M3D-Official-Troubleshooting-Self-Help-Guide_dzE73kMbIAL/All-Printable-STL-Files_sugSV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).

{% hint style="info" %}
As stated above, the first few M3D Crane printers did come with a 3D printed spool holder, which was designed to hold all 4 of the smaller CMYK filament spools. This design has been upgraded but the 3D printed spool holder is **NO LONGER** included in the box with the printer. We **DO** have the **STL file** for the updated spool holder design. We suggest you download the STL, slice it, and print it to your own specifications.
{% endhint %}

## Endstop Damage:

{% hint style="info" %}
Occasionally things can be damaged during shipping, and or come loose. If you notice that one of your end-stops has broken, you can swap any of the others to replace the Z end-stop as this one is the most important.
{% endhint %}

Endstop damage during shipping

## Before powering on your M3D Crane Series Printer:

You should have received along with your printer, a micro SD card as well as a blue micro SD card adapter. Check the SD card slot on the right side of your Crane Series printer to see if yours was shipped with the SD card already in place. If your SD card is already in place, remove it and replace it before powering it on. The SD card may have been shifted or impacted during shipping and turning on the power with the SD card askew inside could lead to damage.

If your SD card has arrived in a small separate case, simply remove the SD card from it's package and place it into the SD card slot on the right side of your Crane Series printer.

The Crane Series of printers are unique in that they are built with a Duet Maestro board. The Duet board uses the information on the SD card to operate, in a sense the SD card that goes in the slot on the Duet acts like it's hard drive. It is for this reason that should you desire to use an SD card to move your gcode to your printer instead of using Duet Web Control, it's recommended to purchase a second micro SD card and use the SD card slot on the back of the LCD screen.

## Additional information:

After assembly you may have some questions that might be further discussed in our[ Pro Tuning Guide](https://crane.printm3d.com/advanced-tuning-m3d-crane-series/tuning-guide).

{% hint style="danger" %}
Prior to exiting this section, please double check all connections, and place your M3D Crane Dual on a flat surface. Ensure the Power Switch is Off\(O\), double check that your voltage is set appropriately for YOUR area\(consult local authorities if you are unsure\). **Failure to do this can irreparably harm the electronics in your printer.**
{% endhint %}

Once your M3D Crane Dual is complete it should look like this:



Congratulations!! You have assembled your new M3D Crane Dual printer!! Move on to the next section to learn how to add the M3D Crane Dual to your existing network or setup a network from scratch.

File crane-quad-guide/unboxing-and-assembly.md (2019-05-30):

# Unboxing and Assembly

{% hint style="warning" %}
The M3D Crane Quad contains sensitive electronics, delicate mechanical parts, and an electrical heating system. Please exercise all applicable safety precautions and follow this guide closely to avoid damage to your M3D Crane Quad, to avoid injury to yourself or others, and insure proper operation.

Check your Local Supply Voltage and set your printers Voltage accordingly, or risk damage to your printer.
{% endhint %}

## Setting up after unboxing your printer:  

After removing your M3D Crane Quad from the box, remove all the plastic wrapping being careful not to cut any of the sensitive parts of the device, such as the cables. Your M3D Crane Quad should look like this:



Remove the bolts at the bottom of each upright rail, as shown below. Setting them aside briefly:

note the bolts sticking out of the rails





{% hint style="warning" %}
Inspect your M3D Crane Quad for any damage that may have occurred during shipping. Every precaution has been made to prevent this, however it is advisable to give all the components a thorough inspection before operation. If any issues are discovered, document the damage by taking an image of the affected area and contact M3D immediately.
{% endhint %}

As long as no issues are discovered, you are ready for mechanical assembly.

## Assembly:  

Being careful not to stress or pull any of the cables, have a friend assist you in raising the upright rails; be sure to **align the bolt holes**.

If you aren't able to hold the upright in place, get someone's help to steady it. Line up the bolt holes \(that previously housed the bolts you removed\) and begin slowly tightening the bolts; first hand tighten, then slowly tighten more firmly with the provided **Allen Key**.



Ensure that all motor cables are connected. These are part of the **black ribbon cable**. You can identify the correct motor cable by looking at the **yellow tags reading 'X, Y, and Z'.** The motor connections are made up of 4 wires, while the associated endstop cable is a three wire cable directly beside the 4-wire cable for the respective motor; the only motor without an endstop is the extruder.





Connect the two gray ribbon cables labeled '1' and '2' and connect them to their respective ports on the back of the LCD assembly, 'EXP1' and 'EXP2'. **Be careful not to cross these connections as it may damage the LCD Screen.**





Should you find that your LCD cables are not labeled, simply determine which cable is **shortest**, that will be the cable to be connected to **EXP1**.

Determine which is Shortest

EXP1

Connect the **short cable to EXP1**, plug the **longer** **cable into EXP2**, and proceed to the next step.

Plug the Short Cable into EXP1 and the Long Cable in EXP2

After making the connections, use the provided bolts and Allen Key to secure the LCD to the front of the M3D Crane Quad.



## Z-endstop positioning:

Be sure your M3D Crane is powered off and/or unplugged before you begin this step.

In order to ensure nothing is damaged during shipping, and furthermore during the first power on of your M3D Crane, it's been shipped with the Z-endstop raised. You will need to manually lower your Z-endstop before printing.

Z endstop

The first step to moving your Z-endstop to an appropriate height is to examine the exposed bolts below the Y-carriage and to tighten/loosen all four of your bed nuts so that only about 8-10 threads are exposed on each. You can see in this photograph a bolt that has been tightened to its recommended position. Use your own 7mm or 1/4th inch wrench to ensure each bolt is adjusted to approximately the same position.

8-10 threads exposed

Next you will need to manually center the print head over the bed. To do this gently move the print head left-to-right along the X-axis until it's in the center. Then, move the bed forward along the Y-axis until its center. At this point, the print head should be above the center of the bed. Finally, rotate the coupler between the Z-motor and the Z-leadscrew counter-clockwise until the left bracket of the X-axis is resting on top of the Z-endstop switch as seen in the photo.

Rotate the Coupler between the Z-motor and the Z-leadscrew

left bracket of the X-axis is resting on top of the Z-endstop switch

The Z endstop is attached to the rail with two T-nuts that hang the inside of the aluminum extrusion channel. Loosen the Z endstop bracket enough to loosen the 2 screws that secure the bracket to the rail.

After loosening the Z-endstop and allowing it to move down, we are now free to move the printhead closer to the bed. Slowly lower the print head until the nozzle touches the bed.

Little by little raise the Z endstop until a click is heard/felt and then tighten down the 2 screws again. You should be able to secure one of the nuts fairly easily to maintain the position of the Z endstop.

Manually raise your print head by rotating the Z axis and now you are ready to power on the M3D Crane and select Home All in the LCD menu. While it is still necessary that we run through the leveling process with the printer powered on, making these changes ensures that we do not cause any damage to the print surface.

In order to assure your M3D Crane Series printer maintains an accurate bed level after following the [Bed Leveling](https://crane.printm3d.com/~/edit/drafts/-LTi556ASBKSVfOwPujM/crane-bowden-guide/manual-bed-leveling) section of this guide it may be necessary to make further adjustments to the Z endstop position. Maneuvering the Z endstop in conjunction with following the Bed Leveling guide will lead to a more accurate and level print bed.

## X Bracket Alignment and tightening:

Should you notice your x bracket, the plate attaching the print head to the x axis is loose OR too tight follow the instructions in the pro-tuning guide to learn how to loosen or tighten the eccentric nuts that secure the x bracket to it's axis.

[https://crane.printm3d.com/advanced-tuning-m3d-crane-series/tuning-guide](https://crane.printm3d.com/advanced-tuning-m3d-crane-series/tuning-guide)

Should your x bracket appear warped or bent, please be sure to check that the eccentric nuts are not too tight. It should be secure enough so that then print head doesn't move around during printing about 1/16-1/12th turn extra past this point on the eccentric nuts should be sufficient any tighter could result in the appearance of warping or bending of the x bracket. Loosing these eccentric nuts should remedy this.

## Rubber Feet:

If your Crane is shipped without the feet assembled, please follow this videio instruction guide

{% embed url="https://photos.app.goo.gl/GswVwPuHoBw8vemBA" caption="" %}

## Crane Spool Holder:

This new Spool Holder design is much more simple. It's a **SINGLE** small spool holder, which is meant to slip into the back facing groove in the top rail of your M3D Crane Series printer. You can print just one, however we do recommend you print up to 4. Having the Spool Holders as singles allows for more mobility, you can now move each spool holder along the axis so as to help control the filament's path to the Quad print head.

### Spool Holder 2.1

Spool Holder 2.1

There is the original Spool Holder design meant to hold up to 4 Micro Spools.

### Spool Holder 1.0

Spool Holder 1.0

### **Additional Information:**

**It is not necessary to print the Spool Holder using CMYK filament**, in fact it's recommended you use the spool holder as one of your first "test prints". This will allow you to accurately calibrate your machine, make sure it's level and is printing properly using a filament you are most comfortable with such as a generic PLA for example.

You can also download [both Crane Spool Holder STL files](https://coda.io/d/M3D-Official-Troubleshooting-Self-Help-Guide_dzE73kMbIAL/All-Printable-STL-Files_sugSV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).

{% hint style="info" %}
As stated above, the first few M3D Crane printers did come with a 3D printed spool holder, which was designed to hold all 4 of the smaller CMYK filament spools. This design has been upgraded but the 3D printed spool holder is **NO LONGER** included in the box with the printer. We **DO** have the **STL file** for the updated spool holder design. We suggest you download the STL, slice it, and print it to your own specifications.
{% endhint %}

## Endstop Damage:

{% hint style="info" %}
Occasionally things can be damaged during shipping, and or come loose. If you notice that one of your end-stops has broken, you can swap any of the others to replace the Z end-stop as this one is the most important.
{% endhint %}

Endstop damage during shipping

## Before powering on your M3D Crane Series Printer:

You should have received along with your printer, a micro SD card as well as a blue micro SD card adapter. Check the SD card slot on the right side of your Crane Series printer to see if yours was shipped with the SD card already in place. If your SD card is already in place, remove it and replace it before powering it on. The SD card may have been shifted or impacted during shipping and turning on the power with the SD card askew inside could lead to damage.

If your SD card has arrived in a small separate case, simply remove the SD card from it's package and place it into the SD card slot on the right side of your Crane Series printer.

The Crane Series of printers are unique in that they are built with a Duet Maestro board. The Duet board uses the information on the SD card to operate, in a sense the SD card that goes in the slot on the Duet acts like it's hard drive. It is for this reason that should you desire to use an SD card to move your gcode to your printer instead of using Duet Web Control, it's recommended to purchase a second micro SD card and use the SD card slot on the back of the LCD screen.

## QuadFusion Print Head: Replacing the Nozzle

Upon shipping your M3D Crane Quad's QuadFusion print head will be fully assembled. Should you wish to replace the nozzle, or should you have taken apart the print head for any reason, follow this Video Guide closely in order to correctly re-assemble your QuadFusion print head.

{% embed url="https://youtu.be/qIrvyc5NEUs" caption="" %}

{% hint style="info" %}
Pay close attention to the Rotational Alignment of the Nozzle upon re-assembly.
{% endhint %}

## Additional information:

After assembly you may have some questions that might be further discussed in our[ Pro Tuning Guide](https://crane.printm3d.com/advanced-tuning-m3d-crane-series/tuning-guide).

Once your M3D Crane Quad is complete it should look like this:



Congratulations on completing the assembly of your M3D Crane Quad printer!! Please continue on to the next section where you will learn how to add your M3D Crane Quad to your existing network, or set up a network from scratch.

{% hint style="danger" %}
Prior to exiting this section, please double check all connections, and place your M3D Crane Quad on a flat surface. Ensure the Power Switch is Off\(O\), double check that your voltage is set appropriately for YOUR area\(consult local authorities if you are unsure\). **Failure to do this can irreparably harm the electronics in your printer.**
{% endhint %}

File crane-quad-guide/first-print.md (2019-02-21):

# First Print

Now that we've covered the very basics on the Duet Web Control Interface, and ran the Bed Leveling Assistant it's time to GET PRINTING. 

## Test Prints: print the test prints first

Before you start slicing and printing your own models it is highly recommended that you print the Test Prints that come pre-loaded for your M3D Crane Series printer. To ensure that your M3D Crane Series printer is operating exactly as intended, we've included several Test Prints that have been created in order to ensure optimal functionality. These test prints are already sliced and ready to go. You can access the Test Prints via the LCD screen Menu.

{% hint style="warning" %}
While it is necessary to use CMYK filament in order to use the Crane Quad's color mixing function, it's NOT necessary to use CMYK filament at all times. During the first few calibration prints, as with all printers SOME experimentation is to be expected and you may go through filament while you are getting to know your new printer. We suggest using a filament you are most comfortable with to start. Our test prints have however been sliced with ABS-R in mind.   
{% endhint %}

### To access the Test Prints: 

* Select **Prepare**
* Move the knob to scroll through the Menu and Select **Test Prints**
* Select **Basic Test Print**

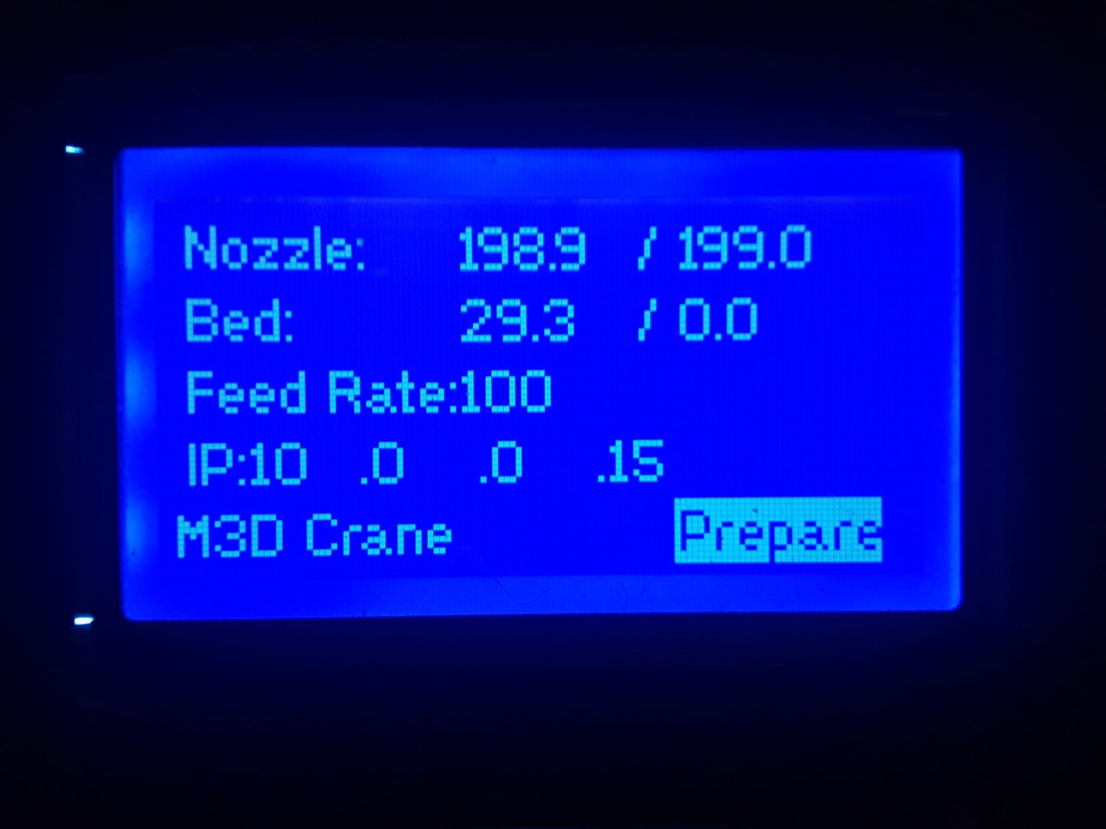
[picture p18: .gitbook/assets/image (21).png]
Select Prepare


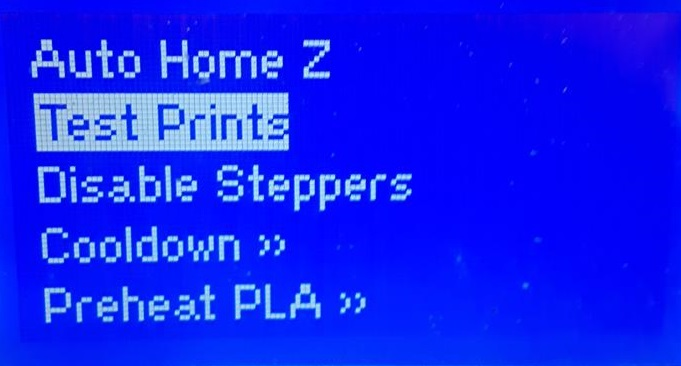
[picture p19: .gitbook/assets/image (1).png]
Select Test Prints


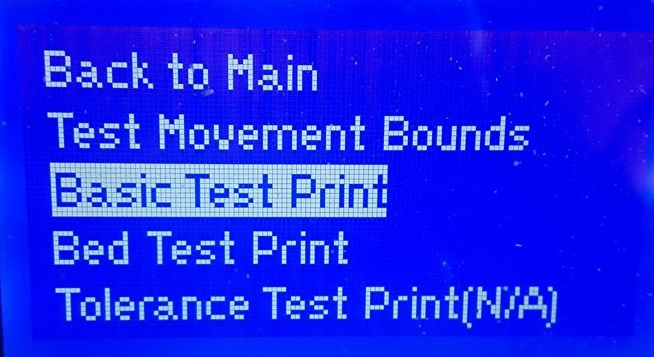
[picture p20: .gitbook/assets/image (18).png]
Select Basic Test Print


The Test Print will start running once selected. It may take several moments to start as the bed and the nozzle will need to get up to running temperature. Be sure to save detailed images of your Test Prints!

## Uploading and Printing:

In the **upper right corner** of the Duet Web Control Interface click on the **Upload and Print** button. 

Upload and Print

When you click on the **Upload and Print** button it will open a window that allows you to choose which gcode file you want to upload. The file will then be uploaded and the printing process will begin. 

The bed as well as the nozzle will begin to heat up according with the settings contained within the gcode file provided by your slicer, and once it's up to temp the print will start.  

## Print Status:

Near the **lower left corner** of the Duet Web Control Console there are tabs. Underneath the Machine Control tab will be **Printer Status**. 

Duet Web Control Interface Print Status

Clicking on the Print Status tab will open a Print Control screen where you can monitor many aspects of your print as well as make changes in real time during the printing process. 

{% hint style="warning" %}
It's recommended that you do not make any changes without first doing further reading so as to not inadvertently cause damage to the print OR your M3D Crane Series Printer.   
{% endhint %}

## Printing Your Spool Holder:

As stated in the first section of this Guide, the Crane Quad no longer comes with the 3D printed spool holder in the box. We do provide the STL file of the updated single spool holder in the Unboxing/Assembly section and it's been included here as well. Because the Spool Holder is a single, it's much smaller and a fairly easy print to experiment with. This print will help you get to know your printer and help you calibrate it. You can download the STL here:

{% file src="../.gitbook/assets/078802\_b1\_crane\_spool\_holder-1.stl" caption="Crane Quad Single Spool Holder" %}

 You **DO NOT** need to use CMYK filament in order to print with your Crane Quad, unless you're wishing to use it's color mixing function. For calibration or test prints it is suggested you use a filament you are most comfortable with. 

Congratulations on your first print with your new M3D Crane Quad printer!! The possibilities are seemingly endless with the M3D Crane Quad, not only will you experience exceptional print quality but you can now do so in stunning, vivid color! You can now experiment with a variety of different colors and materials which will open even greater avenues of creativity and expression.

## Operator notes:

The Crane Quad print head comes with an exceptionally strong fan. Be aware that if you are having difficulties with layer adhesion, or are getting "crunchy" prints you may need to LOWER you fan setting to 15%. 

Feel free to contribute to our ever expanding catalog of user submissions to share your knowledge and experience with the M3D Crane Quad color mixing print head as we continue to grow together as a 3D printing community by following the [Community Submissions and Attributions](https://crane.printm3d.com/community-submissions-attributions/community-submissions) section of this guide. Also don't forget to check out the Advanced Tuning for M3D Crane Series section of this guide for more information.

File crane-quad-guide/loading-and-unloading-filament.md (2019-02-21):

# Loading and Unloading Filament

## **Loading and unloading Filament:**

{% hint style="warning" %}
Warning before loading:

Verify that wiring between the Duet 2 Maestro and the M3D Crane \(including wiring to the QuadFusion and other printer components\) is correct.Verify that the Duet 2 Maestro firmware is updated to the most recent version. You can find version 2.O2 release candidate [here](https://github.com/dc42/RepRapFirmware/releases/download/2.02RC2/DuetMaestroFirmware.bin).In addition you can find the latest version of Duet Web Control [here](https://github.com/dc42/RepRapFirmware/releases/download/2.02RC2/DuetWebControl-1.22.3.zip).Be sure to double check that the cold section fan 1 is running at full power. \(This is needed for long term heatbreak cooling\)
{% endhint %}

## Pre-loading Process

* Start by cutting your filament flush. You should start with 4 new strands. **\(poorly cut filament may damage PTFE or bind up in the curved path\)**
* Observe port labeling 0-3 and select extruder drive 0 \(If unlabeled, they are in left to right order and the left most will be extruder drive 0\) or if your Quad is labeled from 1 to 4, simply swap the 0 for 1 and proceed as directed. 
* Select a feed rate of 5 mm/s \(any faster and it may shred the filament or cause the motor to skip\)
* Select a 10 mm filament feed amount

{% hint style="warning" %}
**Be sure to set the temperature to 170C** **Not doing this will cause backflow up the nozzles chambers that will block future loadings!**
{% endhint %}

## **Loading Sequence for Duet Web Control** 

1. Insert your chosen filament in to each port and hold it at a curved angle and apply some pressure so the filament remains in it's port once you let go. \(Use the natural curve of the filament to match the curves shown below to minimize any risk of missing the curve path\)

   

2. Once each port has it's respective filament in the loading position start the extrusion sequence as follows: Port 0: 23mm  Port 1: 28mm   Port 2: 28mm   Port 3: 23mm
3. Once each filament has moved down through the print head to the Staging area, directly above the PTFE insert, set the feed amount to 20mm and then Extrude ALL. 
4. Select Extrude ALL again
5. Select Extrude ALL again and at this point filament should start to extrude through the nozzle. 

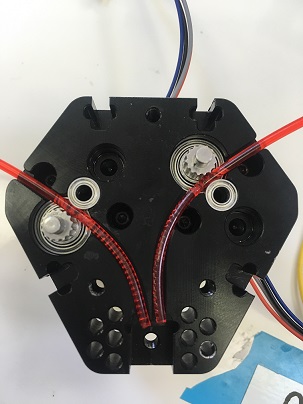
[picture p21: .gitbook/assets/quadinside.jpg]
Filament Staging Area


If you experience ANY stalling at ANY stage of the filament loading process it is advisable to STOP, retract and try again until you can complete all of the steps without any interruption. Should you experience persistent stalling during any step of the loading process please scroll down and refer to the section titled "Stalling during the loading process" for further instruction. 

{% hint style="info" %}
Note: If your Quad print head is not labeled from port 0 to 3, but instead is labeled from 1 to 4 simply swap the 0 for 1 and proceed with the loading sequence as directed.   
{% endhint %}

IMPORTANT: Should you experience ANY stalling during any of the steps above, it is advised that you simply follow the steps to **retract** each filament and start the process over until you are able to move through each step without interruption. 

## Stalling during the loading process:

Should you experience frequent stalls during this process refer to the below information to determine exactly when and where the stalls are occurring:  

 Stall during STEP 2, it is occurring in the Quad's block, or filament path.

Stall in STEP 3, it is occurring at the PTFE entrance or within the PTFE insert it's self.

 Stall in STEP 4, it is occurring at the Metal Insert entrance or within the metal insert.

Stall in STEP 5, it is occurring after the metal insert, toward the nozzle tip.

Once you have determined the most likely location of the source of the stalling, you will then be able to clear any blockages and resume your loading sequence. 

## Extrusion: 

* Set the temp to 240C \(nozzle may ooze ignore it\)
* Change settings to extrude all at 15mm/s and leave the extrude amount at 20mm.
* Confirm your temperature is still set to 240C.
* Hit extrude \(Waiting between steps\) until filament comes out at a steady speed.
* Be sure that no motors are skipping 

## Unloading: 

* Set Nozzle Temperature to 170C.
* Change setting to Extrude All, Extrude at 15mm/s and set the extrusion amount at 100mm
* Press retract 3 times
* The machine may now be turned off

{% hint style="info" %}
Turning Off your machine: ****There are no special considerations for turning off your QuadFusion. However, keep in mind that filament should not be above temperature without motion for longer than 5 minutes, with the exception of PETG; which can handle being held at temperature in the QuadFusion for at least one day. PLA readily degrades.
{% endhint %}

## Operating Notes:

While you DO need to use your CMYK filament in order to produce the color mixes it is NOT necessary when you're just wishing to do single color prints. In order to operate your Crane Quad printer with any less than 4 filaments you will need to have at least 30 mm of filament loaded into each of the unused ports. 

The Crane Quad is designed as a 4 filament, color mixing print head. It needs filament in each of it's ports to prevent back flow. This does not mean that  you can not use the Crane Quad for single color or single filament prints. Simply adjust your setting appropriately when you slice your model, and make sure your Quad print head is loaded properly in that there is filament in all 4 ports, regardless if  you intend to utilize each of them or not.

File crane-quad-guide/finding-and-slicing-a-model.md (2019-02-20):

# Finding and Slicing a Model

## Slicing and Printing the first model: 

You may choose to create your own 3D models with software such as [Autodesk's Fusion 360](https://www.autodesk.com/products/fusion-360/overview), or[ Openscad](http://www.openscad.org/downloads.html), however you may wish to start printing models that are already available for download. You can find free models for 3D printing at [Thingiverse](https://www.thingiverse.com/), or you can try a few from [this list](https://all3dp.com/1/free-stl-files-3d-printer-models-3d-print-files-stl-download/).

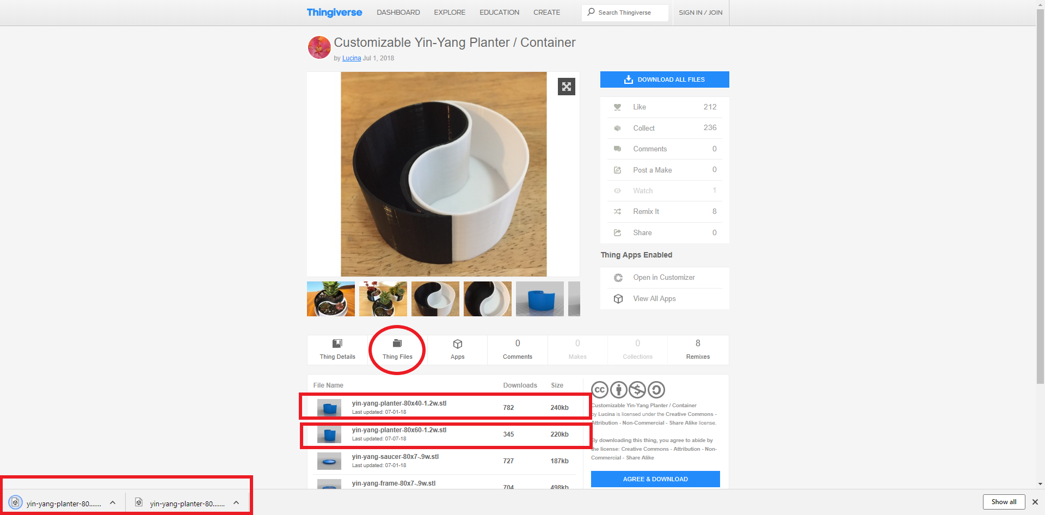
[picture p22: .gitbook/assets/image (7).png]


Once you have found your ideal 3D model and downloaded it's **STL** file, it's time to download a **Slicer**. A **slicer** takes a 3D drawing \(most often in .STL format\) and translates this model into individual layers. It then generates the machine code \(g.code\) that the **printer** will use for **printing**.

While there are several great Slicers out there, both free as well as paid we recommend [Cura](https://ultimaker.com/en/products/ultimaker-cura-software). Download and install the latest version of **Cura by Ultimaker**. Cura will provide a wizard so that you can add your M3D Crane Series printer's dimensions and nozzle diameter

Cura

The M3D Crane Bowden has several Cura **Printing Profiles** that have been pre-configured, each to the optimal settings within Cura for a selection of different material types. You can find and download the first of those here within this point release:  [https://github.com/PrintM3D/Crane/releases/tag/1.1](https://github.com/PrintM3D/Crane/releases/tag/1.1) -- you can also find the latest version of the Bowden SD Card here in case you need it.

Once you have selected and downloaded the Cura Printing Profile you will need for the material you are printing in, you can **Import the profile into Cura and Save it.** You can find these options in the Menu Bar at the top of the slicer's window. For additional information on Cura settings please go [here](https://ultimaker.com/en/products/ultimaker-cura-software).

Now that your settings are optimized with the imported printer profile, you can slice your model. Simply click the "**prepare to print**" button in the lower right corner of the slicer to generate your g.code. **Save this new file to your computer.** 

Your model is now saved on your hard drive. Just follow the instructions for how to use your [Duet Web Control Interface](https://crane.printm3d.com/~/drafts/-LMGnnAn5_tvVgYh8GkJ/primary/v/master/duet-web-interface-new), to learn how to upload your new STL file. Enjoy watching your models come to life! 

## **Color Printing for the M3D Crane QuadFusion:**

The M3D Crane QuadFusion is unique among consumer FDM printers in that it’s able to mix and produce a huge range of color. In order to take full advantage of your M3D Crane QuadFusion’s stunning color range you’ll need to prepare your model for color printing.  

There are a few full color models available online already and you may wish to start out or experiment with those at first. Full color models will already be broken up into several different STL files, all of which will assemble when uploaded into your slicer.  

If you already have a model in mind, but it's not already separated or prepared for color printing you will need to do so yourself using MeshMixer or Blender. You will need to select and separate the different sections of your model into separate facegroups, or shells and save them all separately. 

Depending on your slicers capabilities, you may be able to assign color to each separate part of your assembled model. You may need to utilize a tool such as MeshMixer or Blender however to assign colors or texture maps to your model.Within your slicer you will then assign an extruder to each of the color sections of your model. Depending on the slicer, you may be able to assign a color to each extruder. This could be the natural color of the filament or in some slicers you'll be able to assign a mixed color. Once you are happy with the colors you have assigned to each extruder, you will need to color your model. Simply make sure you assign the extruder with the color you want, to the section of the model that corresponds.  

## **Voxelizer: A most capable color mixing slicer**

As we pioneer color mixing technology, we rely on other services and software to rise to the challenge and innovate along side us. One of the more reliable and easiest to use slicer for color mixing out there is Voxelizer. They offer a free trial period as well as very reasonable subscription fees. Voxelizer is by far the best slicer for the job of color mixing there is currently. We recommend downloading Voxelizer and experimenting with the slicer to experience it for yourself. 

{% embed url="https://voxelizer.com/" %}

When you download and set up your Voxelizer account you will see that our M3D Crane Series printers already have a printer profile. 

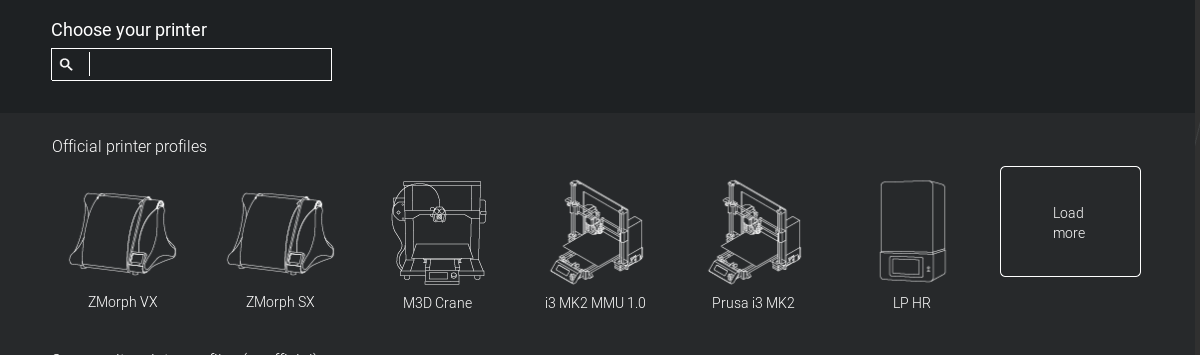
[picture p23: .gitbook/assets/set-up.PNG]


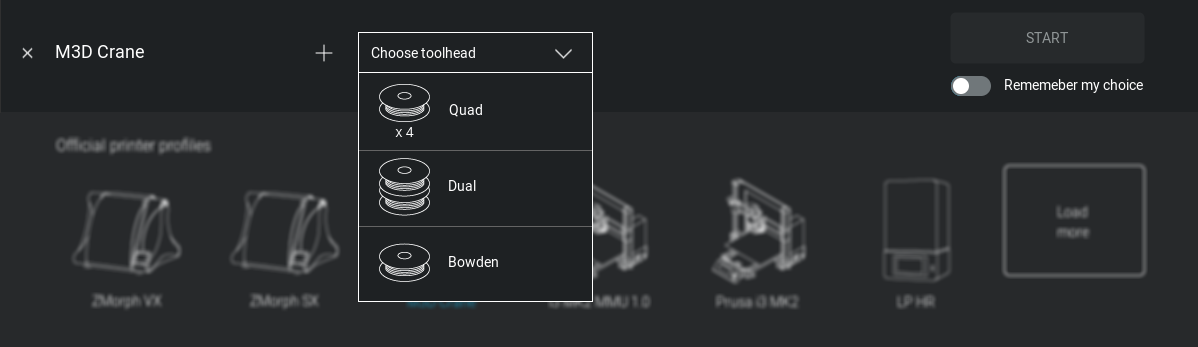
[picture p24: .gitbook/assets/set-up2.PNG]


You can choose from each of the three Crane Series models, and those profiles will automatically contain the standard settings for each of the Crane Series printers, so you will not have to go through each setting setting manually. From these preset printer profiles you'll be able to explore the slicer on your own by adjusting or customizing the presets, adding and assigning color to your model, and even creating custom color blends, and filament profiles. 

Voxelizer is an extremely powerful tool. The information covered here hardly scratches the surface of what all you can accomplish with it. As our user base grows, and more and more start to utilize this powerful new color printing tool we'll all gain by a sharing of information, the swapping of tips and tricks as well as more basic tutorials. 

We have some User Submitted videos on Voxelizer here:

{% embed url="https://www.youtube.com/watch?v=7Q91v6DK9gc&t=11s" %}

{% embed url="https://www.youtube.com/watch?v=0dmPRjeNWpk" %}

**Please return soon for more in depth and up to date information as we ready more tools to enable your M3D Crane Quad-fusion to realize it’s full color mixing potential.**    

Now that we've covered the basics of finding, coloring, and slicing your 3D models, you are ready to make your first print using the M3D Crane Quad printer! The next section will guide you through your first print!

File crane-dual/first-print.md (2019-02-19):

# First Print

Now that we've covered the very basics on the Duet Web Control Interface, and ran the Bed Leveling Assistant it's time to GET PRINTING. 

## Test Prints: print the test prints first

Before you start slicing and printing your own models it is highly recommended that you print the Test Prints that come pre-loaded for your M3D Crane Series printer. To ensure that your M3D Crane Series printer is operating exactly as intended, we've included several Test Prints that have been created in order to ensure optimal functionality. These test prints are already sliced and ready to go. You can access the Test Prints via the LCD screen Menu.

{% hint style="warning" %}
While it is necessary to use CMYK filament in order to utilize the color mixing function of your Crane Dual, it is NOT necessary to use CMYK filament at all times. It is recommended that during the first few experimental stages, while you are getting to know you printer that you use a filament you are most comfortable with. Our test prints have been sliced with ABS-R in mind.  
{% endhint %}

### To access the Test Prints: 

* Select **Prepare**
* Move the knob to scroll through the Menu and Select **Test Prints**
* Select **Basic Test Print**

Prepare

Test Prints

Basic Test Print

The Test Print will start running once selected. It may take several moments to start as the bed and the nozzle will need to get up to running temperature. Be sure to save detailed images of your Test Prints!  

## Uploading and Printing:

In the **upper right corner** of the Duet Web Control Interface click on the **Upload and Print** button. 

Upload and Print

When you click on the **Upload and Print** button it will open a window that allows you to choose which gcode file you want to upload. The file will then be uploaded and the printing process will begin. 

The bed as well as the nozzle will begin to heat up according with the settings contained within the gcode file provided by your slicer, and once it's up to temp the print will start.  

## Print Status:

Near the **lower left corner** of the Duet Web Control Console there are tabs. Underneath the Machine Control tab will be **Printer Status**. 

Duet Web Control Interface Print Status

Clicking on the Print Status tab will open a Print Control screen where you can monitor many aspects of your print as well as make changes in real time during the printing process. 

{% hint style="warning" %}
It's recommended that you do not make any changes without first doing further reading so as to not inadvertently cause damage to the print OR your M3D Crane Series Printer.   
{% endhint %}

Congratulations on your first print with your new M3D Crane Dual printer!! The possibilities are seemingly endless with the M3D Crane Dual, not only will you experience exceptional print quality but you can now experiment with 2 colors or materials at once which will open even greater avenues of creativity and expression. 

 Feel free to contribute to our ever expanding catalog of user submissions to share your knowledge and experience with the M3D Crane Dual as we continue to grow together as a 3D printing community by following the [Community Submissions and Attributions](https://crane.printm3d.com/community-submissions-attributions/community-submissions) section of this guide. Also don't forget to check out the Advanced Tuning for M3D Crane Series section of this guide for more information.

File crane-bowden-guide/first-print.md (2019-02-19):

# First Print

Now that we've covered the very basics on the Duet Web Control Interface, and ran the Bed Leveling Assistant it's time to GET PRINTING. 

## Test Prints: print the test prints first

Before you start slicing and printing your own models it is highly recommended that you print the Test Prints that come pre-loaded for your M3D Crane Series printer. To ensure that your M3D Crane Series printer is operating exactly as intended, we've included several Test Prints that have been created in order to ensure optimal functionality. These test prints are already sliced and ready to go. You can access the Test Prints via the LCD screen Menu.  

{% hint style="warning" %}
It's recommended when setting up any printer for the first time to expect SOME experimentation in order to get to know your printer. This may consume filament in the process, so we advise you use a filament you are most comfortable with, however our test prints have been sliced using ABS-R. 
{% endhint %}

### To access the Test Prints:

* Select **Prepare**
* Move the knob to scroll through the Menu and Select **Test Prints**
* Select **Basic Test Print**

Select Prepare

Test Print

Basic Test Print

The Test Print will start running once selected. It may take several moments to start as the bed and the nozzle will need to get up to running temperature. Be sure to save detailed images of your Test Prints! 

## Uploading and Printing:

After you have printed the Test Prints it's time to start printing your own models! Here you will be shown how to upload and print via the Duet Web Control Interface. 

In the **upper right corner** of the Duet Web Control Interface click on the **Upload and Print** button. 

Upload and Print

When you click on the **Upload and Print** button it will open a window that allows you to choose which gcode file you want to upload. The file will then be uploaded and the printing process will begin. 

The bed as well as the nozzle will begin to heat up according with the settings contained within the gcode file provided by your slicer, and once it's up to temp the print will start.  

## Print Status:

Near the **lower left corner** of the Duet Web Control Console there are tabs. Underneath the Machine Control tab will be **Printer Status**. 

Duet Web Control Interface Print Status

Clicking on the Print Status tab will open a Print Control screen where you can monitor many aspects of your print as well as make changes in real time during the printing process. 

{% hint style="warning" %}
It's recommended that you do not make any changes without first doing further reading so as to not inadvertently cause damage to the print OR your M3D Crane Series Printer.   
{% endhint %}

Congratulations on your very first print with the M3D Crane Bowden printer! You can look forward to exceptional print quality and lasting reliability from your M3D Crane Series printer.  

Feel free to contribute to our ever expanding catalog of user submissions to share your knowledge and experience with the M3D Crane Bowden printer as we continue to grow together as a 3D printing community by following the[ Community Submissions and Attributions](https://crane.printm3d.com/community-submissions-attributions/community-submissions) section of this guide. Also don't forget to check out the Advanced Tuning for M3D Crane Series section of this guide for more information.

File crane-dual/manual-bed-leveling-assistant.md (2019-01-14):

# Bed Leveling

## **Leveling your M3D Crane Series printer via the LCD menu:** 

### **Before you begin:** 

Your bed may have settled while shipping, so before you level your print bed we recommend using the following process to equalize the tension on the springs as well as freeing any that may be compressed**.**

Grasp each side of the print bed with each hand, palms resting on your print bed surface and your fingers resting on the underside of the bed’s carriage. Simply depress the print bed several times to allow the springs to equalize.

## **Basic Bed Leveling:**  

{% hint style="info" %}
**For optimal Bed Leveling be sure to use this Bed Leveling guide in conjunction with the adjustments made to your Z endstop position in the Unboxing/Assembly section of this guide. Maintaining proper Z endstop positioning as well as following proper Bed Leveling procedures will ensure the most accurately leveled print bed, thus producing higher quality prints.**   
{% endhint %}

Scroll through the LCD main menu and select **Prepare** scroll down select **Bed** **Leveling**. In the sub menu select **Basic Bed Leveling**. 







In order to complete the Basic Leveling process you will need **a piece of paper** or an index card of regular 8.5 x 11 paper thickness.

{% hint style="warning" %}
**IMPORTANT:** **As you begin the Basic Leveling process, there will be only 2 options after each prompt; OK or Cancel. You may not go back, so if you are unsure about any step simply select Exit and begin the process from the beginning.**
{% endhint %}

 Once Basic Leveling is selected, your M3D Crane Series printer will **Home All.** After homing, the print head will lift 50mm, and the bed as well as the nozzle will start to heat to temp.



When your M3D Crane Series printer is finished homing, the print head has moved up 50mm, and both the bed and the nozzle have come up to temp, the next prompt on the Basic Leveling menu will appear: **Clear Nozzle Of Excess Filament.** After clearing the nozzle of any excess filament, select **OK** to be given the next prompt in the Basic Leveling process.



{% hint style="danger" %}
**WARNING: At this point the bed and the nozzle will be up to temp, be sure you take necessary precautions to avoid burns.**
{% endhint %}

 The print head will move to the **Left Front** corner and prompt you to **Adjust the Left Front Bed Nut.**



Place your paper under the print head and adjust the Left Front Bed Nut until you feel a **slight resistance** when you try to move the paper. You should still be able to move the paper, sliding it from front to back while experiencing some resistance from the print nozzle. Use the wrench provided with your M3D Crane Series printer to **adjust the Left Front Bed Nut** accordingly and select **OK** when ready to move on.

{% hint style="info" %}
**NOTE: If you can move the paper too easily and it’s experiencing no resistance then your nozzle is still too far from the build plate, and if you can’t move your paper at all or are experiencing severe resistance then your nozzle is too close to the build plate.**
{% endhint %}

 The print head will then move on to the next point and the LCD will display the next prompt: **Adjust Right Front Bed Nut**. Repeat the process of using the paper to help you adjust the Right Front Bed Nut and select **OK** when finished.



The Basic Bed Leveling sequence will repeat the same prompts for the **Right Rear Bed Nut** and the **Left Rear Bed Nut**. Again, once you are satisfied with these adjustments select **OK** to be given the last prompt in the sequence.





**Check Center Bed Height**, is the last prompt in the Basic Bed Leveling Sequence. When checking the Center Bed Height be advised that at the center the paper should experience **slightly more resistance** than the other points. Once you have checked your Center Bed Height, select **OK** to finish the Basic Bed Leveling Sequence. You may wish to run the sequence several times to fine tune your results.



## **Apply Adhesive:**

Once you have gotten a Basic Level on your M3D Crane Series printer, you may wish to print right away. The Apply Adhesive prompt is given at the end of the Basic Bed Leveling process in order to remind you to add your preferred method of adhesive to your print bed in order to insure snug print adhesion.  



Of course  you may wish to run through the Basic Bed Leveling process several times, it's certainly fine to select OK and move on with or without applying any Adhesive.  

{% hint style="info" %}
**NOTE: If the paper has little or no resistance, or is so tight it threatens to tear rather than be moved, repeat the Basic Bed Leveling process over again until the desired results are achieved.**
{% endhint %}

## Manual Bed Leveling:

In the video below there are detailed instructions on how to manually level the print bed of your M3D Crane Series Printer, as well as instructions on how to adjust your Z endstop. 

{% embed url="https://youtu.be/HsCBaC1FupU" %}

Once you are satisfied with the level on your M3D Crane Series printer, it's time to move on to the next section to learn more about heating your print bed and nozzle.

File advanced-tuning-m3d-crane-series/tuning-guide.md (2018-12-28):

# Pro Tuning Guide

{% hint style="warning" %}
The printer should be turned off, and ideally unplugged, before attempting any tuning. Attempted movement of the printer axis while powered could result in damage to yourself or to the printer. Ensure that the hot end has cooled off completely before attempting any tuning as well.
{% endhint %}

The M3D Crane printer has a number of adjustment points for each axis. In the picture below, the red arrows indicate adjustment points for the frame, the yellow arrows indicate eccentric nuts for adjusting the tension on each axis, and the blue circles indicate the tensioning point for the belts.



Each type of adjustment requires a different set of tools, so review the list below before getting started.

## Tools Required

For frame adjustments:

* 5mm hex key \(allen wrench\)

For eccentric nut adjustments:

* 10mm open end box wrench
* 8mm open end box wrench
* 4mm hex key

For belt tensioning adjustments:

* 6mm hex key \(allen wrench\)
* 12mm socket wrench

## How to Adjust

Before we begin, it is important to understand how each of these adjustment points function.

{% hint style="info" %}
The following frame adjustments were already performed at the factory and are not necessary for most users. You should only need to adjust the frame if you have previously taken the printer apart, or ave adjusted all eccentric nuts and are still experiencing binding at certain points on your axis.
{% endhint %}

**Frame Adjustment**

To adjust the frame adjustment points, you simply loosen the hex nut bolts in the frame \(2 at each point\) with a 5mm hex key and twist the metal frame extrusions slightly. There won't be much movement for most of the adjustment points, and it may feel like it's not moving at all, but it is important to ensure these contact points are equal and square, otherwise your axis may bind or you may have erratic print behavior at the extreme ends of your print volume.

**Eccentric Nut Adjustment**

Moving on to the eccentric nuts - This will be the most common type of tuning you perform on your printer. To begin adjustment of an eccentric nut, you take the 4mm hex key and place it in the hex head of the bolt running through the wheel and the eccentric nut. On the other end, you will place the 8mm open end box wrench and loosen the bolt slightly. It does not need to be very loose, and if it is too loose, that will impact your ability to adjust the eccentric nut effectively. Once the bolt is loosened slightly, you can then take the 10mm open end box wrench and spin he larger nut in between the wheel and the build plate. The nut is offset slightly so that as it spins it applies a different amount of pressure between the wheel and the plate. I recommend spinning the nut around completely at least once to get a feel for how the tension changes as it rotates around the bolt. Don't worry about "over tightening" the eccentric nut, as it doesn't actually tighten at all. It spins freely around the bolt with no threads running through the center. You can adjust the eccentric nut in either direction, so play around with it to get a feel for how it adjusts.

Once you've found the desired tension on the eccentric nut, you will need to tighten the bolt back down using the 4mm hex key and the 8mm open end box wrench using the same process you used to loosen it. You're not trying to tighten the bolt down completely, you're just trying to make it snug enough so that the eccentric nut cannot be moved easily and is held in place. It's important to note that when tightening the bolt, it will slightly tighten up the eccentric nut a little more than what you adjusted it to, so it may take a couple tries before you get the feeling down of how tight each eccentric nut and wheel should be.

## X Axis

Print Head Eccentric Nut



{% hint style="info" %}
When properly tuned, the print head should move easily side to side, but should not wobble front to back, nor should the x chassis wobble front to back on the chassis \(See Z Axis tuning for adjustments of the X Chassis\).
{% endhint %}

### Process

1. Begin by loosening the bolt holding the print head's eccentric nut. 
2. Next, adjust the tightness of the eccentric nut by rotating it until the print head is held firmly in plac.
   1. All 3 wheels should be in contact with the rail when properly adjusted. 
   2. When holding the print head steady, you should not be able to rotate any of the wheels on the print head chassis without also moving the print head. 
3. Move the print head back and forth and attempt rocking it slightly
   1. The print head should move left to right easily and the chassis should not rock front to back.
   2. There may be a small amount of play in the connection of the print head to the bracket. 
      1. If this feels like it's too loose, you can remove the print head by loosening the eccentric nut's bolt until the wheel is loose enough to pop the print head chassis off. There are two screws on the back side of the chassis that you can use to tighten the print head to the print head chassis. 

### Tuning Results

{% embed url="https://www.youtube.com/watch?v=Pd\_XtC2xjJA" caption="" %}

## Y Axis

Build Plate Eccentric Nut



When properly tuned, the build plate should move front to back easily and smoothly, but should not rock or tilt. Having a tight and properly aligned build plate is important for ensuring a level, consistent bed. In addition to the eccentric nut on the build plate, the Y axis can also be adjusted by 4 frame mounting points, but this has been adjusted at the factory and is not necessary for most users. Only the eccentric nut adjustments are covered below.

### Process

1. Slightly loosen the bolt holding the build plate eccentric nut, under the right hand side of the build plate.
2. Adjust the eccentric nut for the Y axis until it the platform feels snug and sturdy, and the wheel cannot move without also moving the build plate. 
3. Ensure the plate can move easily all the way along the Y axis.
   1. If there are any tight spots, you may need to loosen the frame bolts related to the Y axis and re-tighten them evenly.
4. Once the Y axis is moving freely, tighten down the bolt holding the eccentric nut and test the movement once more. 

### Tuning Results

{% embed url="https://www.youtube.com/watch?v=xZTWrpctKZs" caption="" %}

## Z Axis

Z Chassis Left Eccentric Nut



Z Chassis Right Eccentric Nut



When properly tuned, the Z axis \(X Chassis\) should be able to move up and down with one hand and should not rock back and forth any. It should be evenly spaced to the top frame on the left and right side as well. Machine oil, or similar lubricants, can be used on the lead screw to aide in ease of movement. Lubrication of the lead screw plays a substantial part in the ease of movement of the Z axis and should generally be one of the first places you check if you are experiencing binding or rough spots in your Z movement. Under manual force, the movement should be consistent and smooth from top to bottom of the Z axis range.

There are 2 primary points of adjustment \(eccentric nuts\) and 4 secondary points of adjustment \(frame attachment points\). Only the eccentric nut adjustments are covered below.

### Process

1. Move the X Chassis all the way to the top or bottom of the axis \(I recommend bottom\). 
2. Start by loosening the right side eccentric nut to the point that the wheel is still touching the frame, but can spin freely by hand without moving the chassis. 
3. Afterwards, loosen the left side eccentric nut to the same point. 
4. Test the movement of the X Chassis up and down. 
   1. It may be slightly difficult to move at this point due to some minor torquing of the chassis on the lead screw. 
5. Adjust the left side eccentric nut so that it tightens up agains the railing a small amount. 
   1. At this point, the left eccentric nut wheel should be snug against the frame and the right side should still be slightly loose. 
6. Go ahead and tighten up the right side eccentric nut until all three wheels are touching the frame and the wheel can no longer spin freely. 
   1. Each side \(left and right\) should feel tight, but not to the point of inhibiting movement. 
7. Now, you can test moving the X Chassis up and down and feel how it moves. 
   1. There should be no wobble in the front to back direction, and the X Chassis should be capable of moving up and down with minor effort.
   2. You can apply a small amount of machine oil to the 4 channels of the lead screw to aide in movement of the X Chassis. Move the chassis up and down slowly to help spread the oil along the lead screw
8. Tighten back down the bolts on the left and right side eccentric nut bolts and test movement again. 
   1. If the axis movement is too stiff after tightening the bolts, ensure you have not over-tightened them, then follow the above steps to loosen the eccentric nuts slightly in order to provide a little more movement freedom, re-tighten the bolts again, and check once more. 

### Tuning Results

{% embed url="https://www.youtube.com/watch?v=m-G7wQ9EP80" caption="" %}

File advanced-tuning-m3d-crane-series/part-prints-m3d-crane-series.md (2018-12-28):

# Part Prints M3D Crane Series

In order to take advantage of our 3D printers ability to not only create rapid prototypes, but also create functional, durable parts we've included several 3D printed components for our M3D Crane Series of printers.

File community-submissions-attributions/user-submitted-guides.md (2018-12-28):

# User Submitted Guides

## User Created Video Guides:

The following Video Guides were created by the user [**Tylerun**](https://www.youtube.com/channel/UCGeec2CuOivtNfsut2HUH1Q/featured) 

## Firmware Updates:

{% embed url="https://www.youtube.com/watch?v=hO7-jUEo5Q4" %}

## Duet Web Control Interface:

{% embed url="https://www.youtube.com/watch?v=QBarLjX7M\_M&t=332s" %}

## Voxelizer 2 Setup and First Print:

{% embed url="https://www.youtube.com/watch?v=7Q91v6DK9gc&t=2s" %}

## Voxelizer 2 Basic Color Switching:

{% embed url="https://www.youtube.com/watch?v=0dmPRjeNWpk&t=25s" %}

We look forward to adding more Video Guides as well as other user submitted content! If you've created some user content and would like to submit it please refer to the section [**About Community Submissions** ](https://crane.printm3d.com/community-submissions-attributions/community-submissions)in order to have your content reviewed for publication.

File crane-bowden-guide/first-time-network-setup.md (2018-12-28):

# First time Network Setup

Connecting to your M3D Crane Series Printer via your local network is very useful as you get access to the **Duet Web Console**. You can connect your M3D Crane Series Printer to your local network via the **Ethernet port on the Duet Maestro.** Once the network settings are properly configured, you will be able to connect to the **Duet board** and access the **Duet Web Console**.

## First-Time Start-up 

{% hint style="info" %}
The M3D Crane Series printers are pre-configured to easily work with the most common network configuration, **DHCP**. If however you have a more complex network configuration, it may be necessary to further edit your network settings.
{% endhint %}

Pre-configured network settings are loaded onto every SD card before the printer goes out our door, these network settings utilize **DHCP** in order to get an IP address from your router. This should allow your M3D Crane Bowden to connect automatically to your network. 

Once connected via **Ethernet** your ****M3D Crane Series printer will display an **IP address** on it's LCD screen.

IP address displayed on the LCD Main Menu

Once connected via **Ethernet** your ****M3D Crane Series printer will display an **IP address** on the Main Menu of the LCD screen. After your printer has had the time to start up, direct your browser to the address http://&lt;IP address&gt;. If the connection is successful the **Duet Web Control** should be shown. You have completed the network setup. If you are unable to access Duet Web Control you may need to contact your Network Administrator. 

M3D Crane Bowden Duet Web Control Interface

In the next section you will learn how to navigate through the LCD menu of your M3D Crane Bowden Printer.

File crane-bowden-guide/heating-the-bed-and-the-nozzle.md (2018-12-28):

# Heating the Bed and the Nozzle

{% hint style="info" %}
There are several options available to control your M3D Crane Series printer. We recommend using the menus provided within the Duet Web Control Interface, however you can also control it via the gcode tab within the Duet Web Control Interface by typing in gcode commands directly, or you can control your M3D Crane Series printer manually through the menu on the LCD screen. This guide will focus on using the menu options inside the Duet Web Control Interface. The other options will be covered elsewhere in the guide.    
{% endhint %}

## Using Duet Web Control Interface to Heat the print bed:

{% hint style="warning" %}
Prior to every heating of the nozzles or the bed, check the temperature readouts in the _Current_ column on the Duet Web Console. These values should be in the 20°C - 250°C. A value of 2000°C, indicates a problem in the wiring of the thermistor. Fix the issue prior to activating the heaters.
{% endhint %}

Connect to your **Duet Web Control Interface** via your network using the **IP address** your M3D Crane Series printer displayed during the network setup step. Once you are connected, you can proceed to heating up your printer bed. 

In the **Duet Web Console Interface** find the table: _**Tools/Heaters/Extra**_ pictured below. In the row **Bed** __**change the active temperature** from 0C to your **desired temperature** and press **Enter**.



In order to turn the heated **bed off,** set the temperature back to **0** in the **Active** column and press **Enter**.

{% hint style="info" %}
It can take a few minutes for the bed to reach the desired temperature and for the heat to dissipate.
{% endhint %}

You can monitor the heating of your bed in both the **Tools** as well as the **Temperature Chart** sections of the Duet Web Control Interface. The Current column within the Tools section will display the temperatures as they change, and the chart will show you the temperature progression allowing you to easily spot any unwanted spikes or drops in the bed or nozzle.  



## **Heating the Nozzles with Duet Web Console:**

In the **Duet Web Control Interface** find the table **Tools/Heaters/Extra**, pictured below. You will be selecting  **Tool 0**, which represents your nozzle. Once your tool \(**Tool 0**\) is selected, simply change the **Active temperature from 0C to your desired temperature**. 

{% hint style="info" %}
Remember that the tool will only heat up to your set active temperature when the tool is **selected**. 
{% endhint %}



In order to **turn off the heater,** set the tools **active temperature to 0 and press Enter**. Remember that a tool will heat up to the standby temperature when the tool is not selected, but was previously selected. You can see which tool is activated by the underline of the tool name in the Duet Web Console.

Now you know the basics of heating your bed and nozzle it's time to move on to loading and unloading filament!

Once you're confidently able to set the temperatures of the M3D Crane Bowden's print bed and the nozzle it's time to move on to the next section to learn how to load and unload filament.

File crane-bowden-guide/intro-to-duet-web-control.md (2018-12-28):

# First look at Duet Web Control

## Getting to know your Duet Web Control Interface:

Now that the **Network Setup** is complete and you have arrived at the IP address your M3D Crane Series printer displayed during the Network Setup process, you can start to utilize the **Duet Web Control Interface**. There are many aspects you are able to monitor and control before, during and after printing from the Duet Web Control Interface. Here we will go over just the basics needed to get you up and printing as quickly as possible. 

## Duet Web Control Interface First Look:

{% hint style="info" %}
The Duet Web Control Interface provides a comprehensive way to monitor and make changes to nearly all aspects of your 3D printing process. This guide is focused on getting your M3D Crane Series printer up and printing quickly. Links will be provided at the end of this tutorial to allow a more in-depth understanding of all the various functions of the Duet Web Control Interface. 
{% endhint %}

Duet Web Control Interface

## The upper portion of the Duet Web Control Interface will display real time information:



The **Machine Status** section displays the **current axis positions, extruder drive positions, Speeds and Z-probe reading**.

Machine Status

 The **Tools** section provides a place to input and monitor the **temperature** of the various tools such as the **nozzle** and the **bed**.

Tools

 The **Temperature Chart** section will provide a real time chart showing the **temperature increase and decrease of the bed and the nozzle**. 

Temperature Chart

## The Lower portion of the Duet Web Control Interface is Dynamic: 



 It contains the **Main Menu Section**, which is comprised of tabs that display their information/interface in the middle portion of the lower half of the Duet Web Control Interface. Under the Machine Control tab you can find the **Axes and extruder control.** The Lower left portion contains the **User-Defined Macros** section.

Main Menu

## Print Status Tab: 

The **print status tab** will not display any information until a print is started, but once you have uploaded and started a print you will see **real time progress** as well as be able to **make changes in real time** to your print as it's printing, such as **micro stepping** or using the **Fan Control section**, changing **fan speeds and ratios.**

Print Status Tab

 The **Print control** section enables you to **pause, cancel or resume** a print, and allows you to make small adjustments to the Z axis called **Z baby stepping**.

Print Control

 The **File information** section **displays select information about the gcode file you have uploaded** to print.

File Information

## **G-Code Console:**

The G-code console is a vital to an experienced 3D printing user. This tab allows you to enter any RepRap Firmware supported command. The printer will execute any command entered here and print feedback and errors. 

G-code Console

Visit the [RepRap Firmware G-Code](https://reprap.org/wiki/G-code) website to learn more about all possible G-codes. Be careful when entering G-code commands as the printer will execute whatever you command you send it.

**G-code Files**

G-code File Screen

This tab is used to upload G-code files to the Duet board. Use the **Upload G-code File\(s\)** __button in order to upload a _._**gcode** file to the printer in order to print it. Click on an uploaded file in order to print it. You also have the ability to create directories here in order to organize your files. 

## **Macros:**

Macros are useful when you find yourself repeatedly performing a sequence of G-code commands. You can easily put these commands into a macro file and upload it here. Click a macro file in order to execute it.

Macros Screen

User defined macros are stored in this tab. Use the dark-blue **Upload Macro File\(s\)** button to upload **.gcode** macro files. 

## **Filaments:**

Utilize this tab in order to define printer filament settings. This can also be performed in Slicer Software

Filaments Screen

Each loaded filament, once loaded, is automatically saved in a new file called **/sys/filaments.csv**. This file may be enhanced in the future to include usage statistics for different materials.

## **Settings:**

**This tab is one of the most important**. This tab allows you to change the **sys/** directory in your SD card and define other user settings.

Settings Screen

When any future updates are released it may be necessary to access the system files such as **config.g** or a **machine.g** file, you can change the files in the settings tab. The Settings tab includes more tabs:

* General: Includes firmware and web console information
* User Interface: Change the look and feel of the Duet Web Console
* List Items: Includes web page suggested options
* System Editor: A very useful tab to change files in the _sys/_ directory of your microSD card. **You will find the** _**config.g**_ **file here as well as other system G-code files.**
* Machine properties: Defines properties of the different drives \(motors\) of the printer.
* Tools: Defines the properties of the tools.

These are the very basics of the Duet Web Control Interface. We'll go over more about the Macro function during the Bed Leveling Assistant section of this guide, but for more comprehensive and in-depth information on each of the features of the Duet Web Control Interface, click [HERE](https://duet3d.dozuki.com/Wiki/Duet_Web_Control_Manual#Section_Overview).

In our Community Submissions section under User Submitted Guides we also have a Video Guide that touches on the basics of the Duet Web Control. You can find that [HERE. ](https://crane.printm3d.com/community-submissions-attributions/user-submitted-guides#duet-web-control-interface)

Now that you are more familiar with both the LCD navigation menu as well as Duet Web Control, it's time to move on to Bed Leveling which will be addressed in the next section.

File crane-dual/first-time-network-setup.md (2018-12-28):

# First time Network Setup

Connecting to your M3D Crane Series Printer via your local network is very useful as you get access to the **Duet Web Control**. You can connect your M3D Crane Series Printer to your local network via the **Ethernet port on the Duet Maestro.** Once the network settings are properly configured, you will be able to connect to the **Duet board** and access the **Duet Web Control.**

## First-Time Start-up 

{% hint style="info" %}
The M3D Crane Series printers are pre-configured to easily work with the most common network configuration, **DHCP**. If however you have a more complex network configuration set up it may be necessary to further edit your network settings.
{% endhint %}

Pre-configured network settings are loaded onto every SD card before the printer goes out our door. these network settings utilize **DHCP** in order to get an IP address from your router. This should allow your printer to connect automatically to your network. 

Once connected via **Ethernet** your ****M3D Crane Series printer will display an **IP address** on the Main Menu of the LCD screen. 

IP address displayed on the LCD Main Menu screen

After your printer has had the time to start up, direct your browser to the address http://&lt;IP address&gt;. If the connection is successful the **Duet Web Control** should be shown. 

Duet Web Control

You have completed the network setup. If you are unable to access Duet Web Control you may need to contact your Network Administrator. 

Now that the network has been set up it's time to learn how to navigate the LCD menu on your M3D Crane Dual printer. Follow the guide to the next section to learn more about the LCD menu.

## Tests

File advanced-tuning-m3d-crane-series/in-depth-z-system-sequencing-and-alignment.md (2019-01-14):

# In-Depth Z-System Sequencing and Alignment

## Z-System Sequencing and Alignment:

The following video goes over how to insure your M3D Crane Series printer's Z-System is properly Sequenced and Aligned:

{% embed url="https://youtu.be/yKg8IiOue3Y" %}

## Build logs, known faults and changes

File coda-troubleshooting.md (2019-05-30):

# Coda For Troubleshooting

Please visit the [M3D Troubleshooting CODA](https://coda.io/d/M3D-Official-Troubleshooting-Self-Help-Guide_dzE73kMbIAL/Crane-Troubleshooting_suMmY#_lu4jO) for more information such as: 

* General Product _FAQs_ 
* Troubleshooting - Procedures for proper identification of problems, diagnostic tests the user can try at home in order of the most likely issues first, and procedures to solve selected confirmed problems
* Product Specifications 
* Printable Files, SD Card images, Sample Slicer Settings and more...

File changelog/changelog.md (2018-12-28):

# Changelog

## October 30, 2018

+Added LCD menus for all Crane Series printers. LCD menus are specific to each Crane type, Dual, Quad, and Bowden.

+Added a config setting to enable the user to change the direction of their LCD encoder. See general.g

+Added Pause and Resume functionality to each of the Crane Series models, Dual, Quad, and Bowden.

+Multiple actions have been added to the encoder button \(knob\). For example when starting a print the LCD will display a “Print Started” screen with an option to go back when pressed again.

+Added “Test Prints” option to the idle screen of the LCD menu.

+Added a “Test Print” menu, providing 3 test prints to select from. Test Print “draft” model, Bed level test, and Hex test.   

- LCD Menu Issue: Change movement axes and extrusion menus on LCD so that + and - are reversed.

-LCD Menu Issue: Change filament numbering to reflect current drive sticker layout.

-SD/Config Issue: Add community contributions to all models included on the SD card.

## October 26, 2018

##  Initial Release:

+This is initial release \(version one\) of the Change Log for the **M3D Crane Series** of printers. The purpose of this document is to track known issues, feature additions, bug reports and resolutions.

+Added state based instructions to the LCD Menu. While printing/paused, the "Tune" button will now appear on the main display. In an idle state the "Prepare" button will appear in its stead.
